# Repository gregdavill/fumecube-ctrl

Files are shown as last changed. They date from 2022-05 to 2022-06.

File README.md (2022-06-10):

# fumecube-ctrl

A replacement controller for the Purex Fumecube, a HEPA filter based fume extractor unit.

## What

This controller replaces the existing control board and adds WiFi control using esphome based firmware.
The board runs off a 12V supply, just like the original control board, and features a relay to control the AC to the motor.

Motor enable and control signals are level shifted with mosfets and sent to the motor controller.

The device is intended to be paired with home assistant, so that a wireless switch or my phone/laptop can enable and adjust the speed of the fan.

`docs/fix-speed-controller` contains a kicad schematic of the original 555 based controller for reference. It seems like it was designed to operate off both an AC transformer and the +12V supply found in my unit.

## Why

The original control interface for the fumecube is a potentiometer on the front of the unit, which features a DPST switch that enables AC to the motor controller.
Having to dial the speed all the way done to turn the unit on/off is cumbersome. Additionally, the unit is typically placed under my desk, and leaning down to turn the unit on and off just doesn't happen all the time. 

## Features

Because the fumecube is made with a sheet metal shell, the ESP is designed on a separate PCB and should be fitted outside the unit in a small 3d printed enclosure.

## Assembled boards

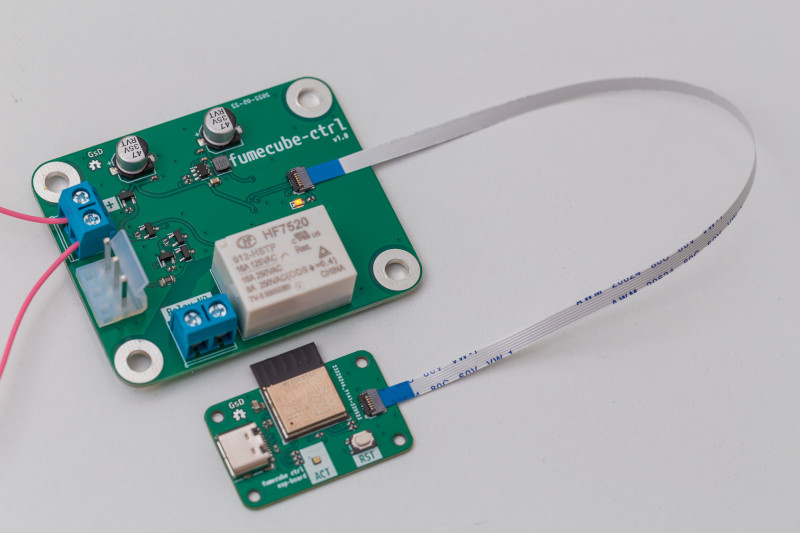
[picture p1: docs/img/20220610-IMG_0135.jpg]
Assembled PCBs


## Firmware

The firmware is based on [ESPHome](https://esphome.io) 
ESPHome projects are defined using a yaml config file. The ESPHome tool then pulls in source files to compile the firmware. You can install it and then compile the firmware with the following:

```
pip install esphome
cd src
esphome compile esp-fumecube.yaml
esphome upload esp-fumecube.yaml --device /dev/ttyACM0
```

## Licence

 * Hardware in this repository is licenced under CERN OHL v1.2

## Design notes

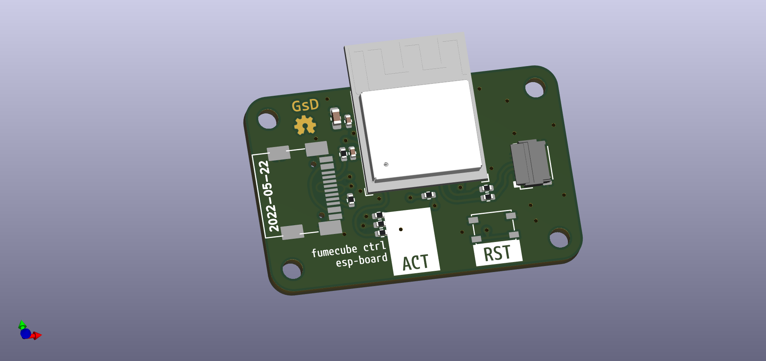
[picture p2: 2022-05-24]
docs/img/esp-ctrl.png

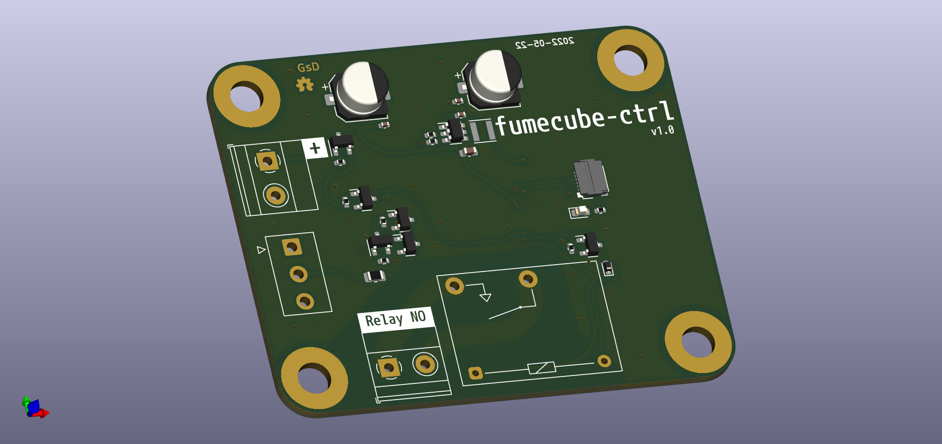
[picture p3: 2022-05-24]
docs/img/fumecube-ctrl.png

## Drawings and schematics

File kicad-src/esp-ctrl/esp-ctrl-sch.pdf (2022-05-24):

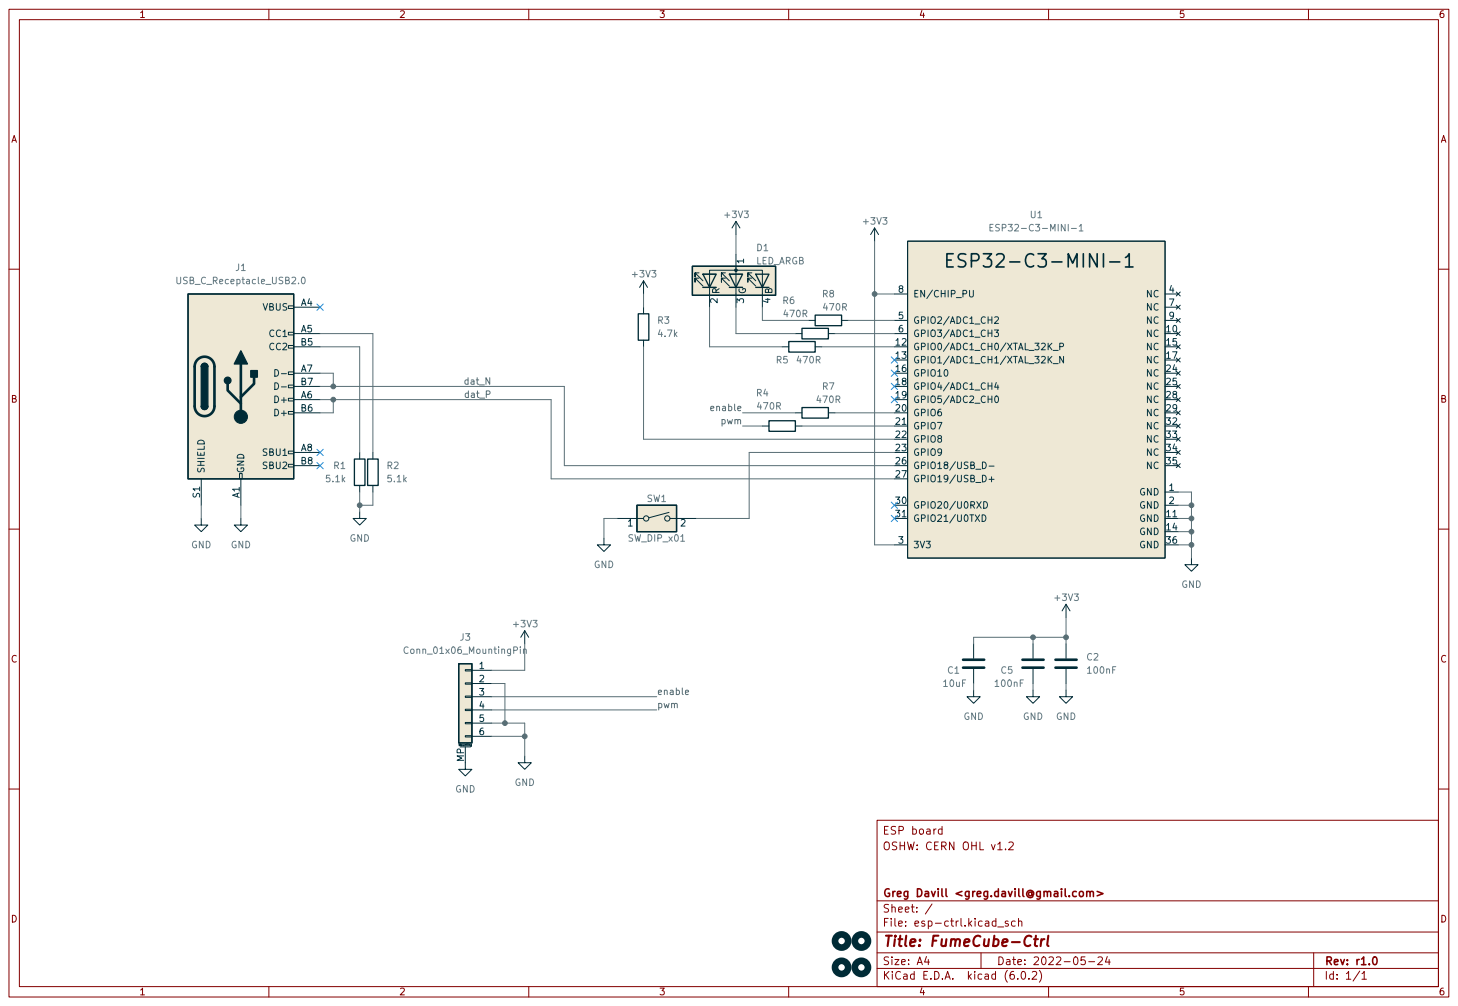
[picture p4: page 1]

File: esp-ctrl.kicad_sch Sheet: / Greg Davill <greg.davill@gmail.com> OSHW: CERN OHL v1.2 ESP board

Id: 1/1 Title: FumeCube-Ctrl

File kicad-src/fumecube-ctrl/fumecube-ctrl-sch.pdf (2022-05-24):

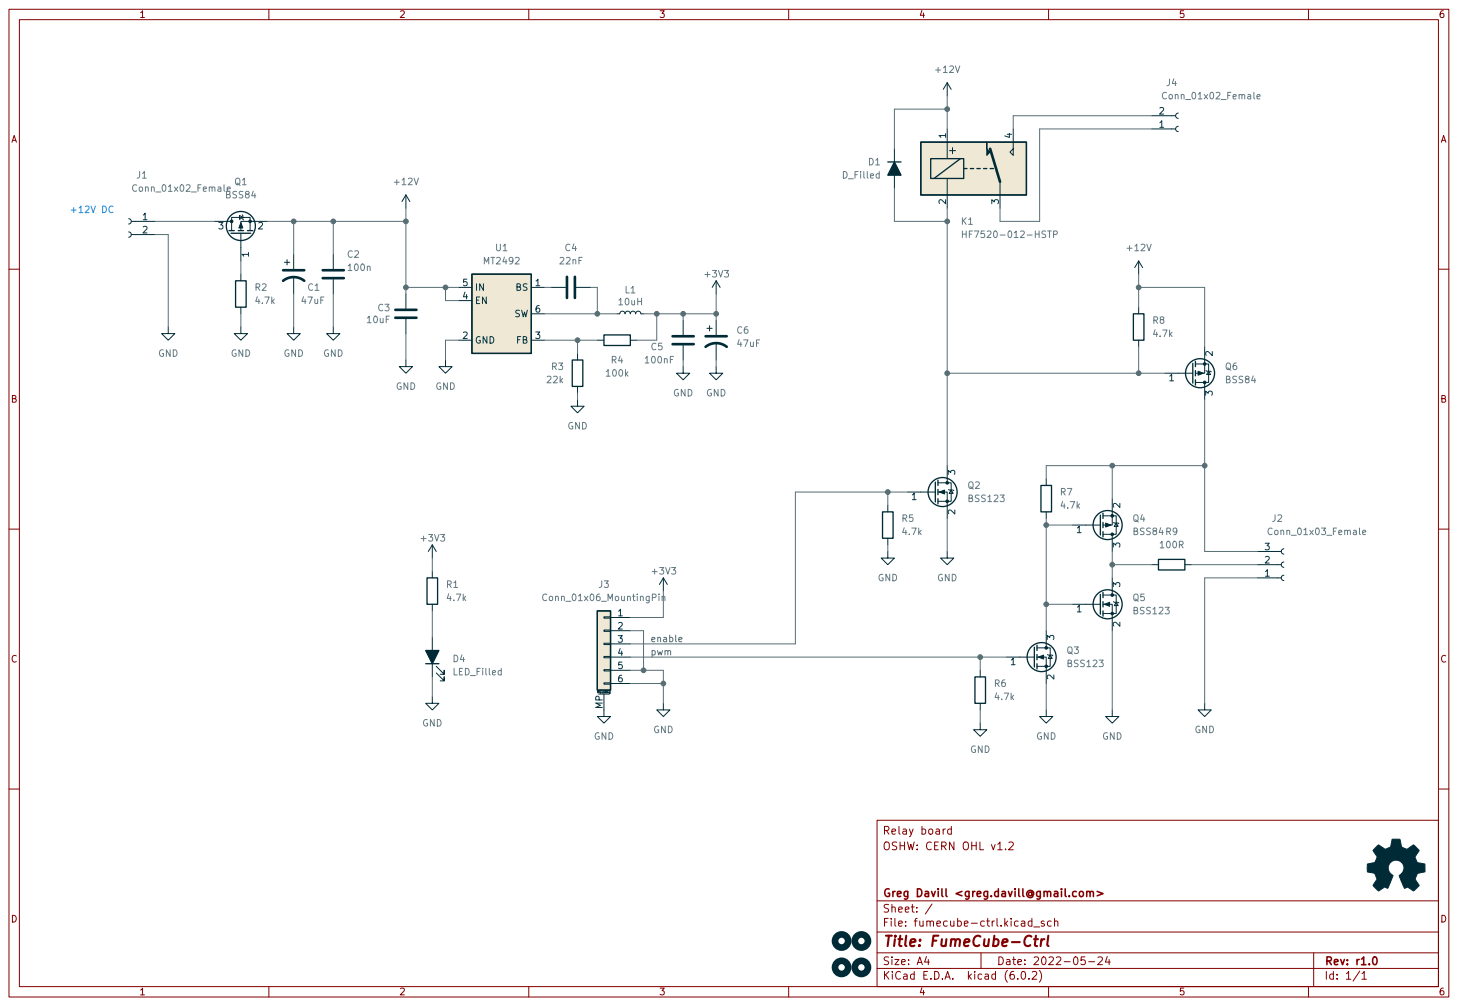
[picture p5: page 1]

File: fumecube-ctrl.kicad_sch Sheet: / Greg Davill <greg.davill@gmail.com> OSHW: CERN OHL v1.2 Relay board GND

Id: 1/1 Title: FumeCube-Ctrl

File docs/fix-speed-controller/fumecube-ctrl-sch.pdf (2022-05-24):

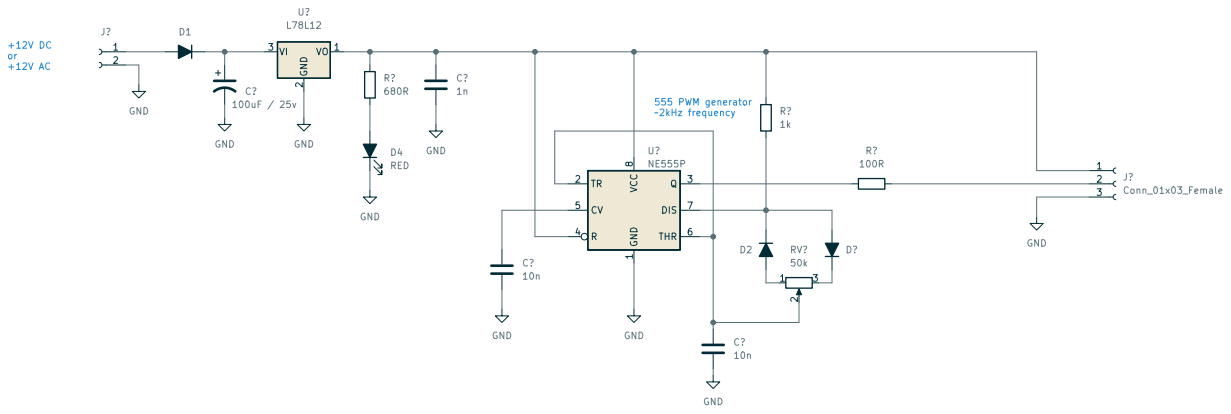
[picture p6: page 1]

Id: 1/1 Title: Fix Speed controller

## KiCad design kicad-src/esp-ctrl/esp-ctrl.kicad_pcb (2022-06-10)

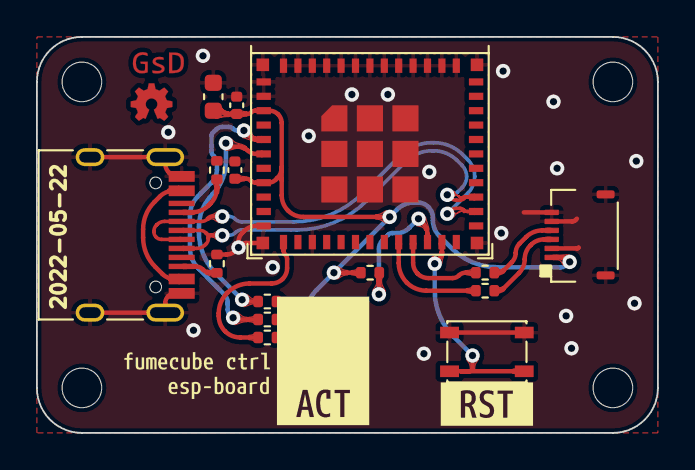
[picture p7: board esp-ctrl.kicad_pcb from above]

Board: 2 copper layers, 34.5 x 22.0 mm, 24 parts (0 on the bottom side), 18 nets.

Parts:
C1: 10uF; C_0603_1608Metric
C2, C5: 100nF; C_0402_1005Metric
D1: LED_ARGB; 0404LED_RGB
H1, H2, H3, H4: MountingHole_Pad; MountingHole_2.2mm_M2_ISO7380
J1: USB_C_Receptacle_USB2.0; USB_C_Receptacle_HRO_TYPE-C-31-M-12
J3: Conn_01x06_MountingPin; Hirose_FH34SRJ-6S-0.5SH_1x6-1MP_P0.50mm_Horizontal
R1, R2: 5.1k; R_0402_1005Metric
R3: 4.7k; R_0402_1005Metric
R4, R5, R6, R7, R8: 470R; R_0402_1005Metric
SW1: SW_DIP_x01; SW_SPST_PTS810
U1: ESP32-C3-MINI-1
kibuzzard-628A11E7: G***; kibuzzard-628A11E7
kibuzzard-628A126A: G***; kibuzzard-628A126A
kibuzzard-628A1224: G***; kibuzzard-628A1224
kibuzzard-628A1254: G***; kibuzzard-628A1254

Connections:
+3V3: C1.1, C2.1, C5.1, D1.1 (A), J3.1, R3.1, U1.3 (3V3), U1.8 (EN/CHIP_PU)
/dat_N: J1.A7 (D-), J1.B7 (D-), U1.26 (GPIO18/USB_D-)
/dat_P: J1.A6 (D+), J1.B6 (D+), U1.27 (GPIO19/USB_D+)
/enable: J3.3, R7.1
/pwm: J3.4, R4.1
GND: C1.2, C2.2, C5.2, J1.A1 (GND), J1.A12 (GND), J1.B1 (GND), J1.B12 (GND), J1.S1 (SHIELD), J3.2, J3.5, J3.6, J3.MP (MountPin), R1.2, R2.2, SW1.1, U1.1 (GND), U1.2 (GND), U1.11 (GND), U1.14 (GND), U1.36 (GND)
unnamed: D1.2 (RK), R5.1
unnamed: D1.3 (GK), R6.1
unnamed: D1.4 (BK), R8.1
unnamed: J1.A5 (CC1), R2.1
unnamed: J1.B5 (CC2), R1.1
unnamed: R3.2, U1.22 (GPIO8)
unnamed: R4.2, U1.21 (GPIO7)
unnamed: R5.2, U1.12 (GPIO0/ADC1_CH0/XTAL_32K_P)
unnamed: R6.2, U1.6 (GPIO3/ADC1_CH3)
unnamed: R7.2, U1.20 (GPIO6)
unnamed: R8.2, U1.5 (GPIO2/ADC1_CH2)
unnamed: SW1.2, U1.23 (GPIO9)

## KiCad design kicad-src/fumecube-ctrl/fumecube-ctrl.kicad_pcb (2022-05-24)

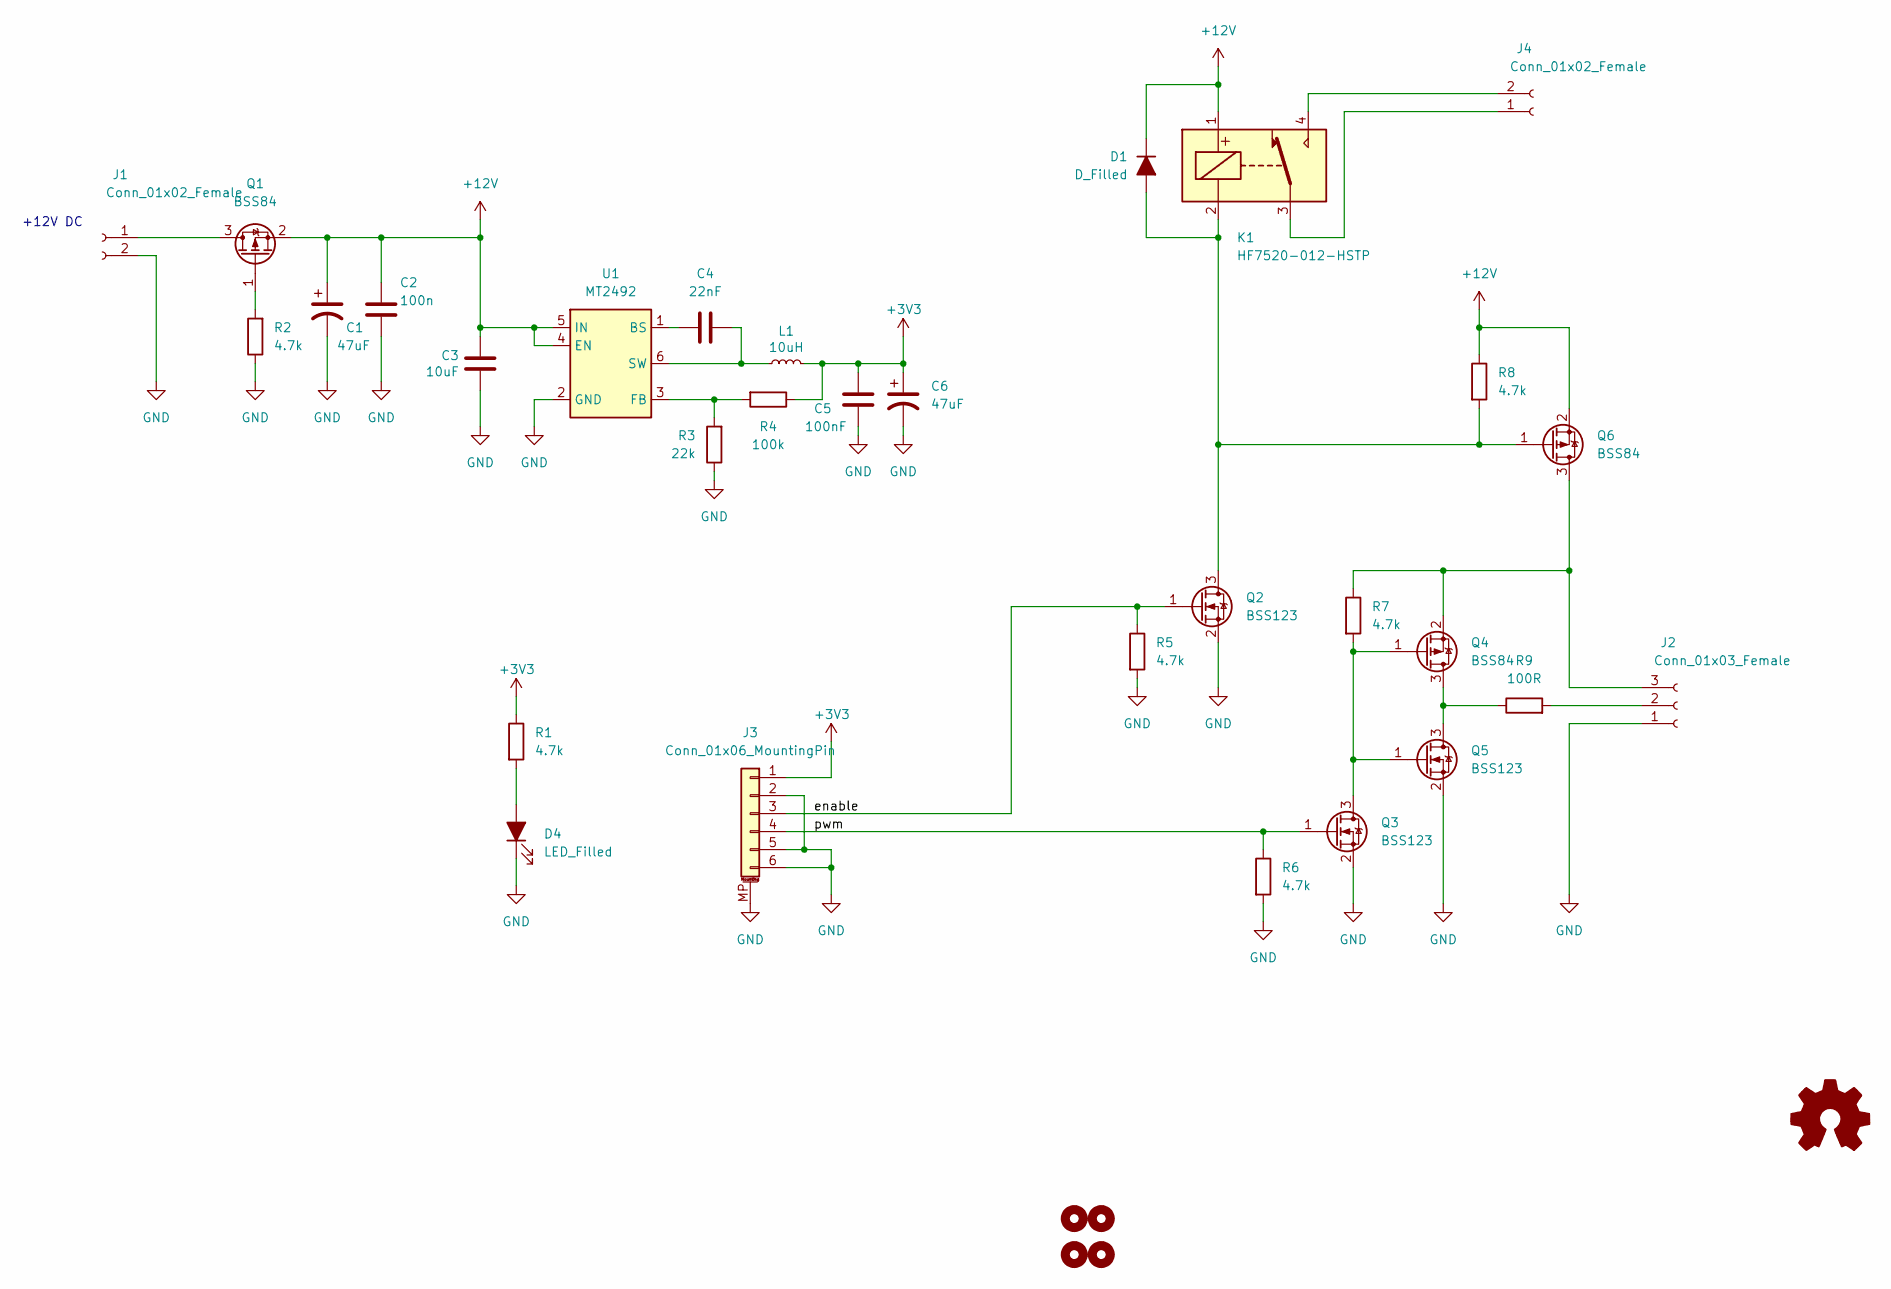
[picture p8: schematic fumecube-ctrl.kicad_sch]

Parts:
C1, C6: 47uF; CP_Elec_6.3x4.5; lcsc C72522
C2: 100n; C_0402_1005Metric
C3: 10uF; C_0603_1608Metric
C4: 22nF; C_0402_1005Metric
C5: 100nF; C_0402_1005Metric
D1: D_Filled; D_SOD-523; lcsc C2965561
D4: LED_Filled; LED_0603_1608Metric; lcsc C84269
H1, H2, H3, H4: MountingHole_Pad; MountingHole_4.5mm_Pad
J1, J4: Conn_01x02_Female; TerminalBlock_Phoenix_MKDS-1,5-2_1x02_P5.00mm_Horizontal; lcsc C474881
J2: Conn_01x03_Female; TE_826576-3_1x03_P3.96mm_Vertical; lcsc C2884053
J3: Conn_01x06_MountingPin; Hirose_FH34SRJ-6S-0.5SH_1x6-1MP_P0.50mm_Horizontal
K1: HF7520-012-HSTP; lcsc C53788
L1: 10uH; L_Taiyo-Yuden_NR-30xx; lcsc C340363
Q1, Q4, Q6: BSS84; SOT-23; lcsc C347485
Q2, Q3, Q5: BSS123; SOT-23; lcsc C699301
R1, R2, R5, R6, R7, R8: 4.7k; R_0402_1005Metric
R3: 22k; R_0402_1005Metric
R4: 100k; R_0402_1005Metric
R9: 100R; R_0805_2012Metric
U1: MT2492; SOT-23-6

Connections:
+3V3: C5.1, C6.1, J3.1, L1.2, R1.1, R4.1
+12V: C1.1, C2.1, C3.1, D1.1 (K), K1.1, Q1.2 (S), Q6.2 (S), R8.1, U1.4 (EN), U1.5 (IN)
/enable: J3.3, Q2.1 (G), R5.1
/pwm: J3.4, Q3.1 (G), R6.1
GND: C1.2, C2.2, C3.2, C5.2, C6.2, D4.1 (K), J1.2, J2.1, J3.2, J3.5, J3.6, J3.MP (MountPin), Q2.2 (S), Q3.2 (S), Q5.2 (S), R2.1, R3.1, R5.2, R6.2, U1.2 (GND)
unnamed: C4.1, U1.1 (BS)
unnamed: C4.2, L1.1, U1.6 (SW)
unnamed: D1.2 (A), K1.2, Q2.3 (D), Q6.1 (G), R8.2
unnamed: D4.2 (A), R1.2
unnamed: J1.1, Q1.3 (D)
unnamed: J2.2, R9.2
unnamed: J2.3, Q4.2 (S), Q6.3 (D), R7.1
unnamed: J4.1, K1.3
unnamed: J4.2, K1.4
unnamed: Q1.1 (G), R2.2
unnamed: Q3.3 (D), Q4.1 (G), Q5.1 (G), R7.2
unnamed: Q4.3 (D), Q5.3 (D), R9.1
unnamed: R3.2, R4.2, U1.3 (FB)

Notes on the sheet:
+12V DC

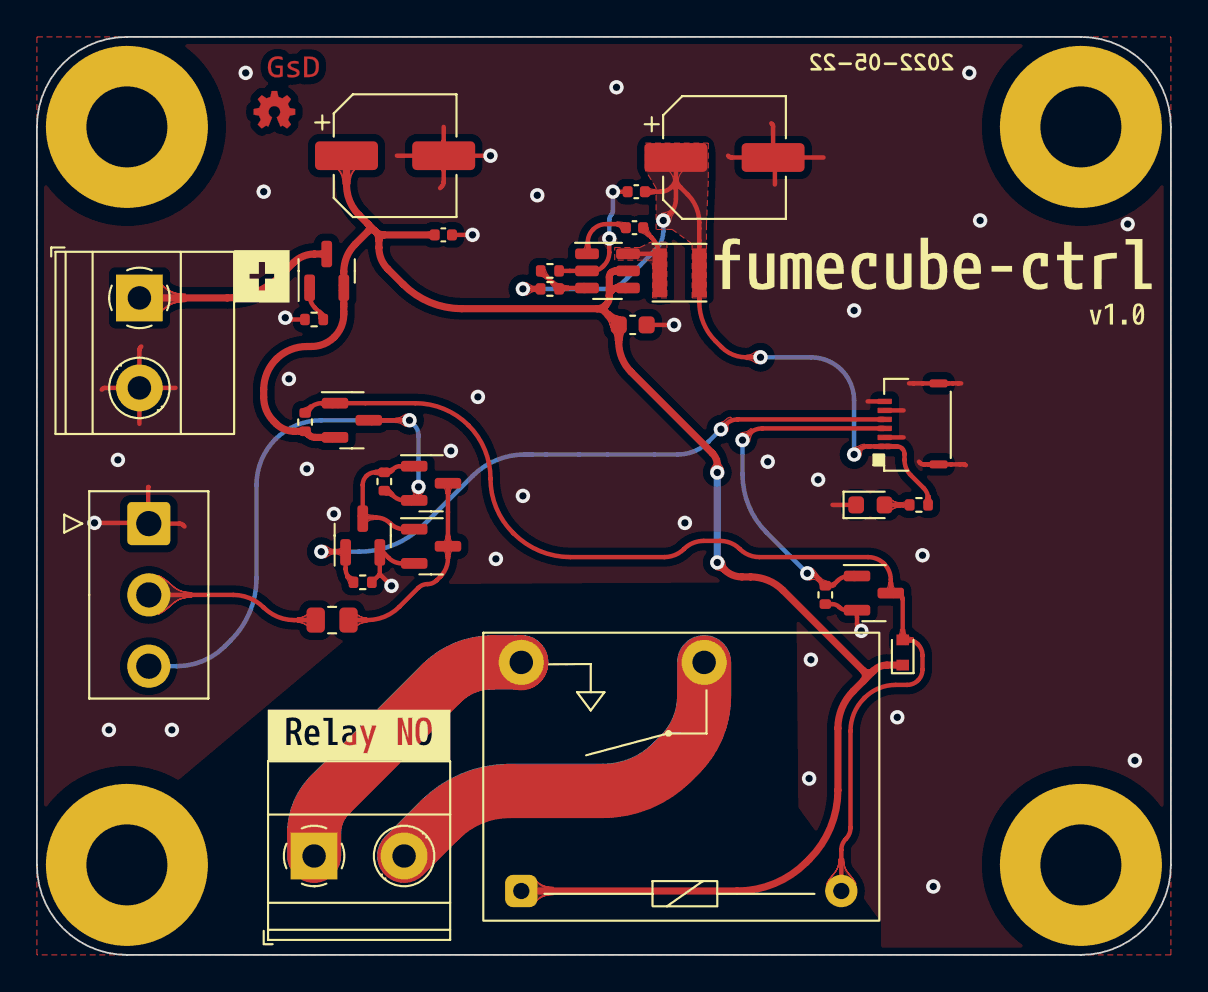
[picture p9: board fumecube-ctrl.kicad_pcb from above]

Board: 2 copper layers, 63.0 x 51.0 mm, 38 parts (0 on the bottom side), 18 nets.

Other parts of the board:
kibuzzard-6289DEB3: G***; kibuzzard-6289DEB3
kibuzzard-6289EB2D: G***; kibuzzard-6289EB2D
kibuzzard-6289EB16: G***; kibuzzard-6289EB16
kibuzzard-6289EB97: G***; kibuzzard-6289EB97

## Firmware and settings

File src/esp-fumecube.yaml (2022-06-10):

esphome:
  name: esp-fumecube
  platformio_options: #https://github.com/esphome/issues/issues/2931
    board_build.flash_mode: dio  

esp32:
  board: esp32-c3-devkitm-1
  framework:
### Arduino
    # type: arduino
    # version: dev
    # platform_version: https://github.com/platformio/platform-espressif32.git#feature/arduino-upstream

### IDF
    type: esp-idf

# Enable logging
logger:
  level: DEBUG

# Enable Home Assistant API
api:

wifi:
  ssid: !secret wifi_ssid
  password: !secret wifi_password
  fast_connect: true

# Enable signal on GPIO6
power_supply:
    id: relay_pwr
    pin: GPIO6

# PWM output on GPIO7
output:
  - platform: ledc
    id: gpio_pwm
    power_supply: relay_pwr
    pin: GPIO7
    #channel: 0
    frequency: 2000Hz

# LED output status out GPIO3
  - platform: gpio
    id: led_green
    pin: GPIO3
    inverted: true
  

# LED status out GPIO2
light:
  - platform: status_led
    id: led_red
    pin: 
      number: GPIO2
      inverted: true

fan:
  - platform: speed
    output: gpio_pwm
    #speed_count: 4
    name: "FumeCube Speed"
    restore_mode: ALWAYS_OFF
    on_turn_on:
      then:
        - output.turn_on: 
            id: led_green
    on_turn_off:
      then:
        - output.turn_off: 
            id: led_green

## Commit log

2022-05-24 Initial commit
    - Add PCB designs
    - Add README
    [XZxxxxxx150W.step, esp-ctrl.kicad_pcb, esp-ctrl.kicad_sch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]
2022-06-10 Update README
    - Add photo of assembled unit
2022-06-10 Update esp-ctrl design
    [esp-ctrl.kicad_pcb]
